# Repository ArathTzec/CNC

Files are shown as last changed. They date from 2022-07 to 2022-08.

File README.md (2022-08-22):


<h1 align="center"> ⚙️ MEJORA EN LA MANUFACTURA DE PLACAS PBC A TRAVÉS DE UNA MAQUINA CNC PARA ALUMNOS DE TSU EN MECATRÓNICA DENTRO DE LA UTEZ ⚙️ </h1>
<h3 align="center">🚀 Ing. de proyectos 🚀</h3>
<h4> Integrantes: </h4> 
<p>- 👷‍♂️ ARZATE VALLE JOSE MARTÍN </p>  
<p>- 👷‍♂️ FLORES FIGUEROA ALEJANDRO </p> 
<p>- 👷‍♂️ REYES ARAUJO ALDO </p> 
<p>- 👷‍♂️ ROQUE MORALES ALEJANDRO </p> 
<p>- 👷‍♂️ TZEC VARGAS ARATH </p>

### CONTENIDO
#### Descripción del proyecto
- 📚 Resumen
- 🏢 Planteamiento del problema 
- ⚙️ Objetivos
  - General 
  - Específicos 
- Justificación
- Alcances
#### Desarrollo
- 📎 Planeación
- Desarrollo del proyecto
  - Definición del proyecto
  - ✍ Boceto
  - 💰 Presupuesto estimado del proyecto
  - 🔨 Definición de partes mecánicas
  - 💻 Investigación de software de calibración de motores
  - 🖊 Diseño en SolidWorks
  - 💲 Compra de materiales
  - ✂ Cortar los perfiles de aluminio
  - 🖨 Impresión de piezas 3D
  - 👁 Verificar y corregir tolerancias de las piezas impresas
  - 🤏 Ajuste y lubricacion de ejes, rodamientos, guias, etc
  - 🔩 Configuracion, calibracion e instalacion del firmware/software
  - ✔ Prueba de funcionamiento 
#### Resultados y conclusiones 
- Resultados
  - Conclusiones y recomendaciones   

<h4 align="center"> DESCRIPCIÓN DEL PROYECTO </h4> 

##### 📚 Resumen 
<p>Actualmente las máquinas CNC se encuentran en una infinidad de aplicaciones a lo largo y ancho del planeta, desde la fabricación de electrodomésticos, pasando por la ebanistería hasta la producción de piezas para automóviles y aviones. Los beneficios de este tipo de tecnología son muchos, tales como: alta precisión en el fresado, permite mecanizar piezas más complejas, alta repetibilidad, los ajustes iniciales son mínimos y reduce al máximo los errores cometidos por el operario, a la vez que no requiere mucha habilidad por parte del mismo. </p> 
<p>Con la creación del prototipo de una máquina-herramienta CNC para el fresado y perforado automático de PCB, se brinda una calidad final muy alta a un costo de fabricación y esfuerzo muy bajo. </p>
<p>La máquina será de gran ayuda para los estudiantes de ingeniería en mecatrónica y todo tipo de personas que se dediquen al desarrollo de productos electrónicos, debido a que les permitirá llevar fácilmente sus circuitos desde la protoboard hasta la placa de impreso, en un tiempo de producción bastante corto. Por lo tanto, desde el punto de vista funcional, económico, y académico práctico, se confirma como necesario la sistematización del proceso de fabricación de placas de circuito impreso. </p>

##### 🏢 Planteamiento del problema
<p>Las PCB son una pieza fundamental en el montaje final de todo tipo de desarrollo tecnológico, ya que permite darle firmeza al circuito y darle una presentación adecuada, lamentablemente cuando los estudiantes requieren llevar de la protoboard a una PCB sus desarrollos se realiza de manera artesanal como el serigrafiado el cual es un método muy costoso, otro método es el de planchado el cual requiere demasiado tiempo y el peor de los casos dibujar manualmente el circuito sobre la placa. Por supuesto el resultado final deja mucho que desear, ya que no es muy presentable o incluso se pueden generar cortocircuitos que no se observaron y por supuesto el uso de cloruro férrico el cual es nocivo para la salud y el medio ambiente. </p> 

##### 🏹 Objetivos

###### General
- Crear una CNC que nos permita hacer PCBs de manera más precisa y con riesgo de falla mínimo.
###### Específicos 
- Realizar el diseño de cada una de las partes que conformarán la CNC.
Realizar la programación de la máquina-herramienta CNC, para fresar y perforar PCB de forma automática.

##### Justificación
<p>La razón de este proyecto es para que los estudiantes puedan pasar el desarrollo de sus circuitos en protoboard a una placa de circuito impreso con riesgo de falla mínimo, mas preciso, barato y en el menor tiempo posible, ya que los métodos empleados actualmente son muy costosos, requieren de mucho tiempo y se usan sustancias nocivas para la salud, por otro lado, la posibilidad de falla por cortocircuito es mayor debido a que en muchos casos no es posible apreciar a simple vista los errores cometidos. </p> 

##### Alcances
<p>Con este proyecto se pretende diseñar, construir y programar un prototipo de máquina fresadora y perforadora para la elaboración automática de placas de circuito impreso, utilizando para ello el control numérico por computador (CNC). La máquina es capaz de fresar placas de una dimensión máxima de 15x25cm, para ello se utilizan motores paso a paso con una resolución de 200 pasos por vuelta en configuración de paso completo. EI intercambio de herramientas en la máquina se realiza de forma manual, ya que por el reducido número de herramientas necesarias para el fresado y perforado de las PCB, no se hace necesario implementar un intercambiador automático.<p>
  
<h4 align="center"> DESARROLLO </h4> 

##### Planeación
<p>En la siguiente tabla se presenta el Diagrama de Gantt de las actividades a realizar en el proyecto.<p>
 
 |       Actividad       | S1 | S2 | S3 | S4 | S5 | S6 | S7 | S8 | S9 | S10 | S11 | S12 | S13 | S14 |
 |-----------------------|----|----|----|----|----|----|----|----|----|-----|-----|-----|-----|-----|
 |Definición de proyecto | X  |    |    |    |    |    |    |    |    |     |     |     |     |     |
 |Elección de proyecto   |    | X  |    |    |    |    |    |    |    |     |     |     |     |     |
 |Boceto del proyecto    |    |    | X  |    |    |    |    |    |    |     |     |     |     |     |
 |Presupuesto            |    |    | X  |    |    |    |    |    |    |     |     |     |     |     |
 |Inv. software de motores|   |    |    | X  | X  |    |    |    |    |     |     |     |     |     |
 |Diseño en SolidWorks   |    |    |    |    | X  | X  | X  |    |    |     |     |     |     |     |
 |Compra de materiales   |    |    |    |    | X  | X  |    |    |    |     |     |     |     |     |
 |Cortar perfiles de aluminio| |   |    |    |    |    | X  |    |    |     |     |     |     |     |
 |Impresión de piezas 3D      |    |    |    |    |    |    | X  |    |     |     |     |     |     |
 |Verificar y corregir tolerancias| | | |    |    |    |    | X  |    |     |     |     |     |     |
 |Ensamble de la CNC     |    |    |    |    |    |    |    |    | X  |     |     |     |     |     |
 |Ajuste y lubricación   |    |    |    |    |    |    |    |    |    |  X  |     |     |     |     |
 |Configuración e instalación de firmware/software|||||||   |    |    |     |  X  |     |     |     |
 |Entrega                |    |    |    |    |    |    |    |    |    |     |     |     |     |  X  |
  
##### Desarrollo del proyecto
<p>En esta sección se describe paso a paso todo el procedimiento que se llevó a cabo para el diseño de una CNC con el objetivo de mejorar la manufactura de PCBs y reducir los riesgos de falla.<p>

###### Definición de proyecto
<p>Para comenzar en la realización de este proyecto se pensó en una máquina que diera solución alguna problemática y se eligieron a los integrantes adecuados para formar un equipo de alto rendimiento.<p>

###### Elección de proyecto
 <p>Ya que hemos definido hacia dónde va el proyecto, se dieron varias propuestas que se muestran a continuación:<p>
   
  |         Integrante        |                Prouesta               |
  |---------------------------|---------------------------------------|
  | Arzate Valle Jose Martín  | *Maquina CNC*                         |
  | Flores Figueroa Alejandro | Sistema de llenado y sellado de bolis |
  | Reyes Araujo Aldo         | Protección para soldadura de mano     |
  | Roque Morales Alejandro   | Sistema de enfriamiento de hielera    |
  | Tzec Vargas Arath         | Compuerta automática para perros      |
   
###### ✍ Boceto
Esta imagen representa el boceto realizado en el software de SolidWorks, de aquí partimos para poder realizarlo en físico

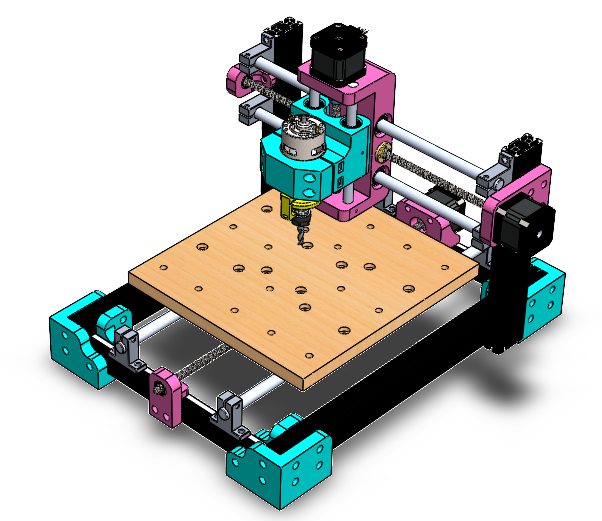
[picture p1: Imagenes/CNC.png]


###### 💰 Presupuesto estimado del proyecto
Aqui podras encontrar el presupuesto y material del proyecto ===> [Presupuesto](https://github.com/ArathTzec/CNC/tree/main/Materiales)
   
###### 💻 Investigación de software de calibración de motores
<p>GRBL es un firmware para el control de máquinas CNC, está pensado para usarse en placas Arduino con un microcontrolador Atmega328, ya que nos permite configurar el control y desplazamiento de nuestra máquina. Los controladores paso a paso se clasifican para una longitud de impulso mínima de paso.<p>
  
###### 🖊 Diseño en SolidWorks
<p>Para realizar el proyecto de manera física, primero se requiere un diseño que ayudará para evitar problemas y proporcionar parámetros para optimizar aspectos cruciales del proyecto. A continuación, se muestra el diseño en el programa SolidWorks:<p>
  
###### 💲 Compra de materiales
<p>Se realizó la compra de los materiales listados anteriormente por medio de tiendas en línea como lo fueron Amazon y Mercado Libre, en la siguiente figura se muestra el material comprado.<p>
  
###### ✂ Cortar perfiles de aluminio
<p>Se cortaron los perfiles de aluminio en medidas de:
  - 2 perfiles de 40 cm
  - 2 perfiles de 25.5 cm
  - 2 perfiles de 24 cm<p>
    
###### 🖨 Impresión de piezas 3D

Las piezas se imprimieron mediante impresora 3D, para más información dirígete al siguiente enlace ===> [Piezas en 3D](https://github.com/ArathTzec/CNC/tree/main/Archivos%20CAD/M%C3%A1quina%20CNC)
  
###### 👁 Verificar y corregir tolerancias de las piezas impresas

Todas las piezas que se imprimen en 3D llegan a tener alguna tolerancia o “error” de impresión, para corregir este error puedes lijar la pieza impresa hasta que los elementos como rodamientos, guías, husillos y tornillos logren entrar correctamente 

###### 🤏 Ajuste y lubricación de ejes, rodamientos, guias, etc.

Para lubricar los componentes se utilizó grasa blanca con litio y aceite. Las siguientes imagenes muestran la colocacion de estos: 

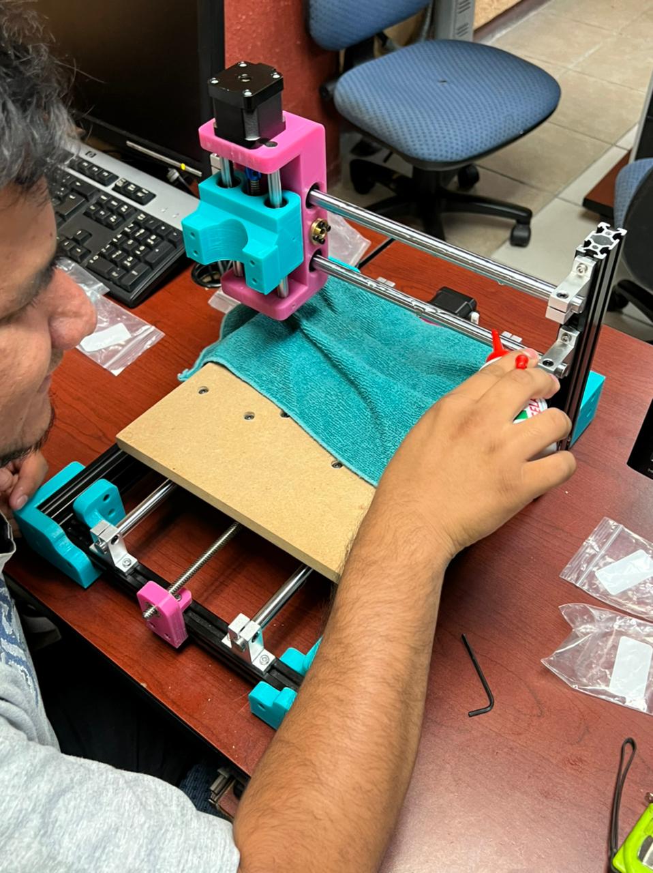
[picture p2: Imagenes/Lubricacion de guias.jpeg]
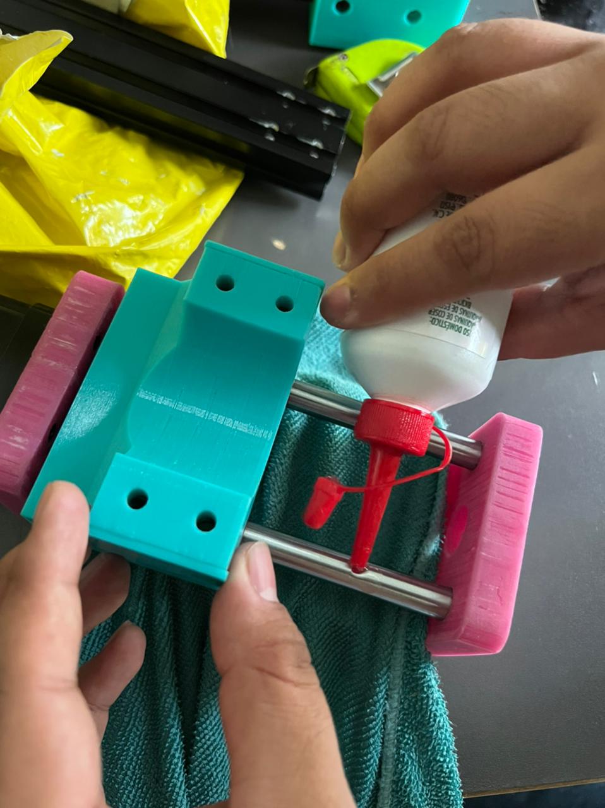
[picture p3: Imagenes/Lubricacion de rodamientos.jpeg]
    

###### 🔩 Configuracion, calibracion e instalacion del firmware/software
 
Puedes consultar como se calibro dando click aqui ==> [Calibracion](https://github.com/ArathTzec/CNC/blob/main/Manuales/Configuracion%20de%20los%20drivers%20para%20el%20motor%20paso%20a%20paso%20.pdf)
 
###### ✔ Prueba de funcionamiento 
En la primera prueba se volvieron a ajustar los motores, debido a que no estaban bien calibrados. También se agrego mas grasa blanca con litio para que los husillos funcionaran de una mejor manera, ya con esta grasa los ejes se pudieron mover correctamente. De la misma manera al hacer estos cambios la maquina funciono mejor 
 
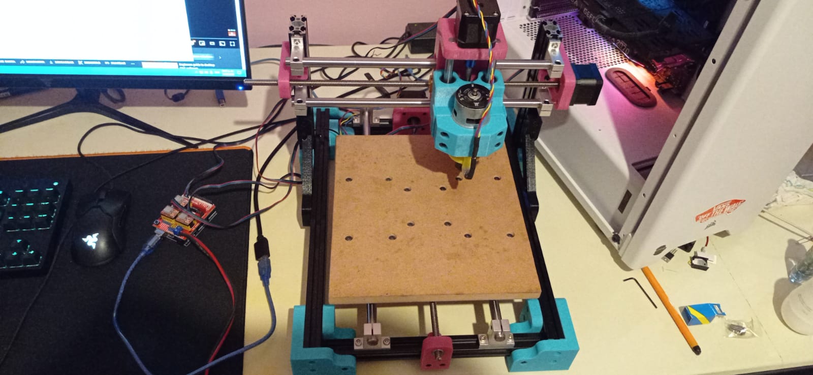
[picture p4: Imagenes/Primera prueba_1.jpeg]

 
##### Entrega de proyecto
 
<h4 align="center"> RESULTRADOS Y CONCLUSIONES </h4> 

Como resultados del proyecto se entrego una maquina CNC que logra mejorar la manofactura de las placas PCB:

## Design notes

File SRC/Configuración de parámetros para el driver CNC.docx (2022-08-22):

Configuración de parámetros para el driver CNC -GRBL

El driver GRBL necesita una configuración previa para funcionar y tener la mejor precisión posible, para esto se configurarán los parámetros del $0 -$22, cabe mencionar que algunos parámetros se colocaron de default.

Dependiendo del motor a pasos que se compró, se buscó el datasheet para visualizar los grados por paso que da el motor, este motor cuenta con 1.8°, pero necesitamos saber cuantos pasos requiere para dar una vuelta, por lo tanto, se tiene lo siguiente:

((un giro completo)360)/1.8=Se requieren de 200 pasos para una vuelta completa

Lo que sigue después es saber dependiendo de la varilla, cuantos milímetros se recorre por cada vuelta, por lo tanto, para las varillas que se compraron se tiene que por cada vuelta recorre 8 milímetros, cuando se divide entre el numero de pasos para dar la vuelta completa del motor queda en 25.

De esta manera se colocan los parámetros del $0 al $3 que corresponden a los pasos por milímetros de los motores x, y z

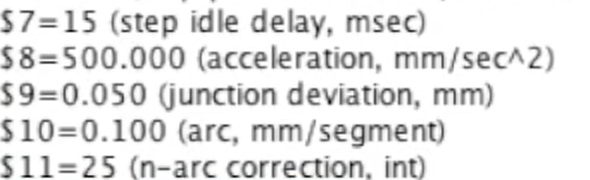
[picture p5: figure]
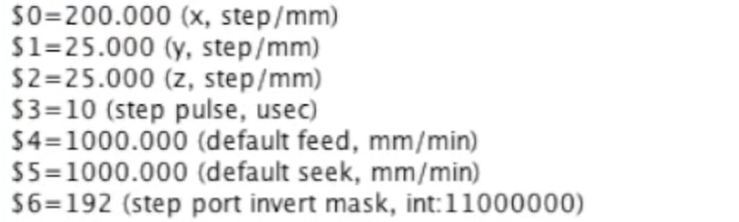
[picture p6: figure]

Después configurar el ancho de pulso que manda el Arduino, se colocó en 10

- Los puntos 4 y 5 corresponden a velocidad del motor, en este caso es de 1000
- 6 no se modifica nada
- 7 es el tiempo de retardo después de realizar alguna orden, se coloco en 15 milisegundos
- 8 la aceleración del motor quedo en 500 debido a que a esa aceleración el motor dejo de vibrar
- 9-11 Se quedaron en default. En el numero 12 se colocaron 3 decimales para mayor precisión.
- 13 se configura todo en milímetros colocando un 1
- 14-18 Default
- 19-20 Se configura la velocidad con la que la maquina vuelve al origen
- 21-22 Default

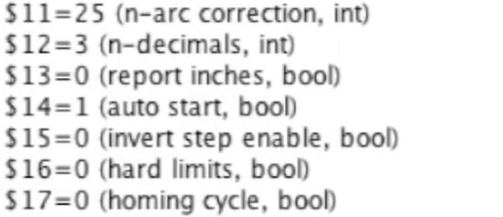
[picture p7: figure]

- La lista queda de la siguiente manera:

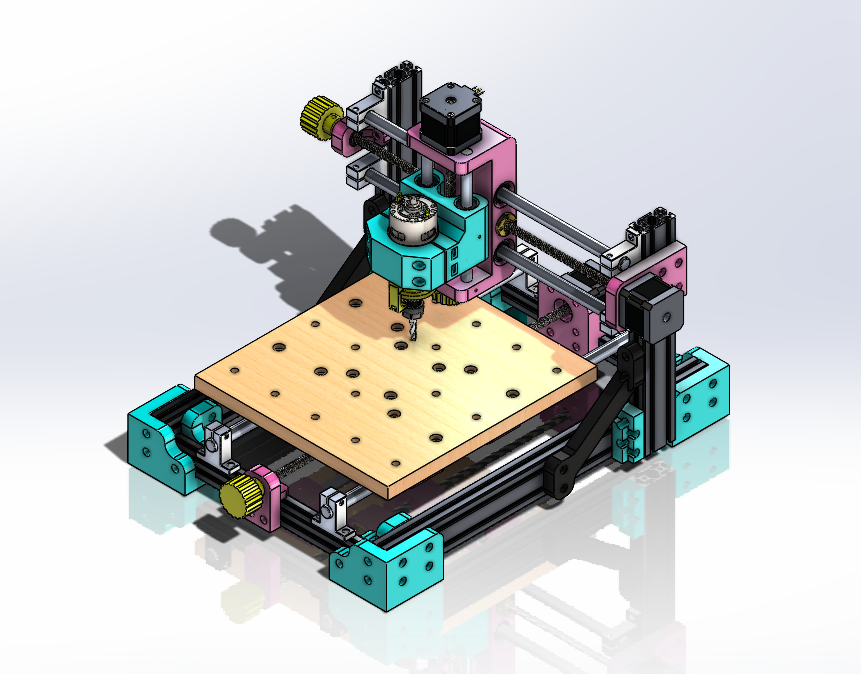
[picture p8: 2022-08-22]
Imagenes/Diseño terminado.PNG

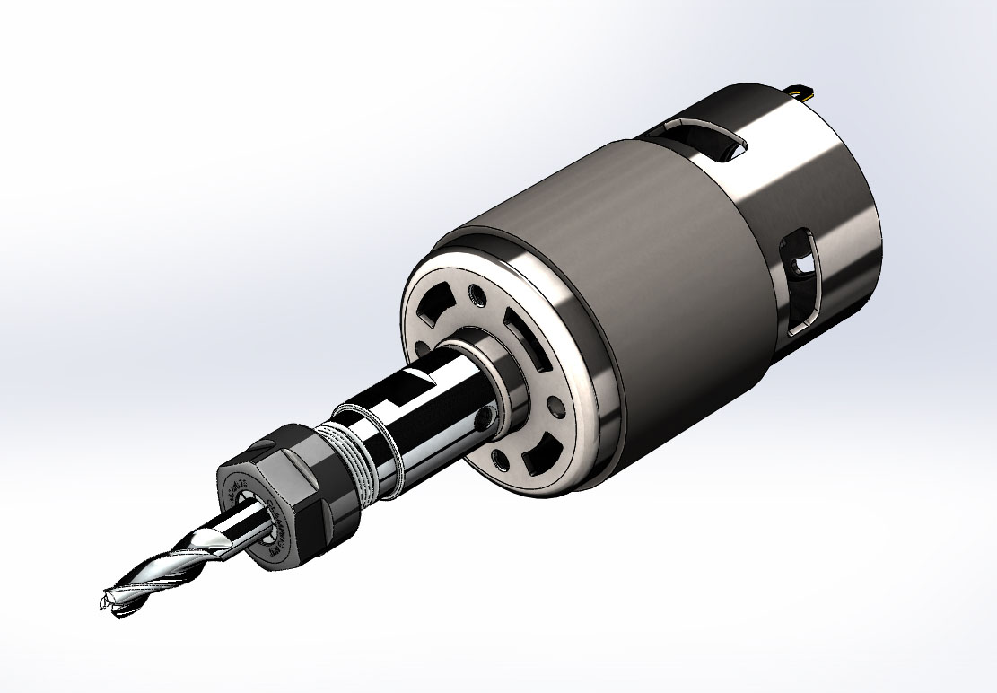
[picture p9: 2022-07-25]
Archivos CAD/Máquina CNC V1.1/Source/Motor CD/Motor - RS-775 - 1.JPG

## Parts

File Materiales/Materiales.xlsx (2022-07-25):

LISTA DE MATERIALES Y PRECIOS DEL PROYECTO
Material | Cantidad | Precio Unitario | Total
Motor DC 755 | 1 | $748 | $748
Motor a pasos | 3 | $170 | $510
Rollo de PETG 1.75mm 1KG | 1 | $449 | $449
Fuente de alimentación 24V | 1 | $409 | $409
Base soporte para riel eje lineal | 4 | $55 | $220
Rodamiento LM12UU | 8 | $65 | $520
Guía lineal 8mm 300mm | 1 | $110 | $110
Perfil aluminio 2080 500mm | 1 | $650 | $650
Perfil de aluminio 2040 400mm | 2 | $258 | $516
Perfil de aluminio 2020 300mm | 6 | $85 | $510
Guía lineal 12mmX1500mm | 1 | $575 | $575
Guía lineal 10mmX300mm | 1 | $230 | $230
Sensor de velocidad | 1 | $150 | $150
Tabla de madera 240mmX160mm | 1 | $200 | $200
Total: |  |  | $5797

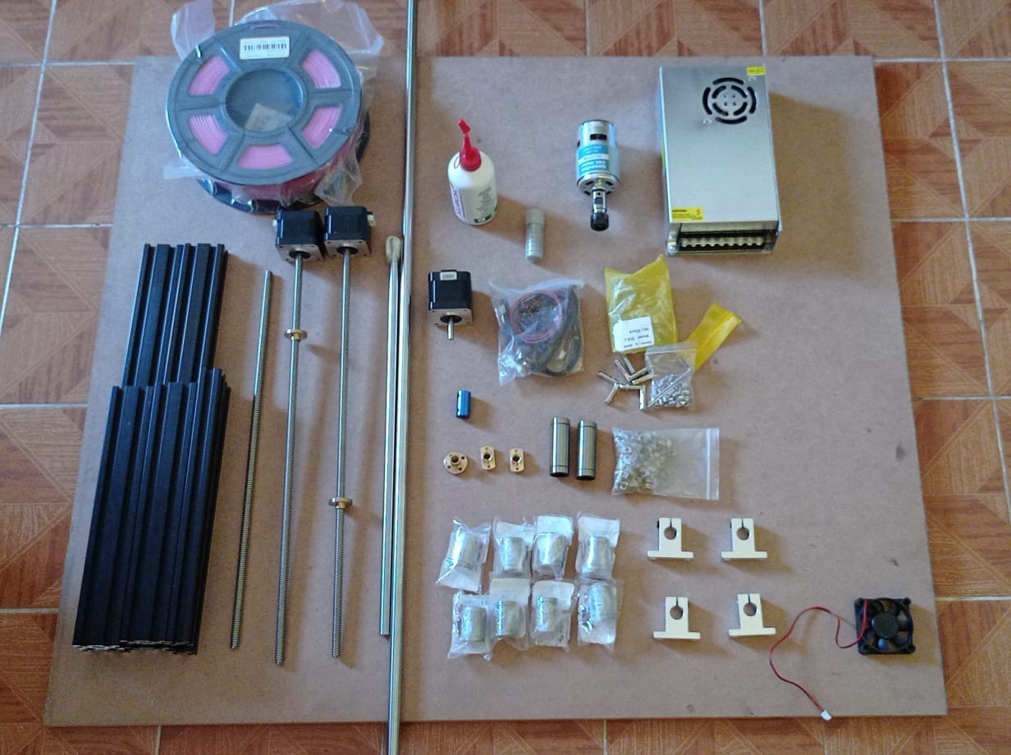
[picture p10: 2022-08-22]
Materiales/Materiales.jpeg

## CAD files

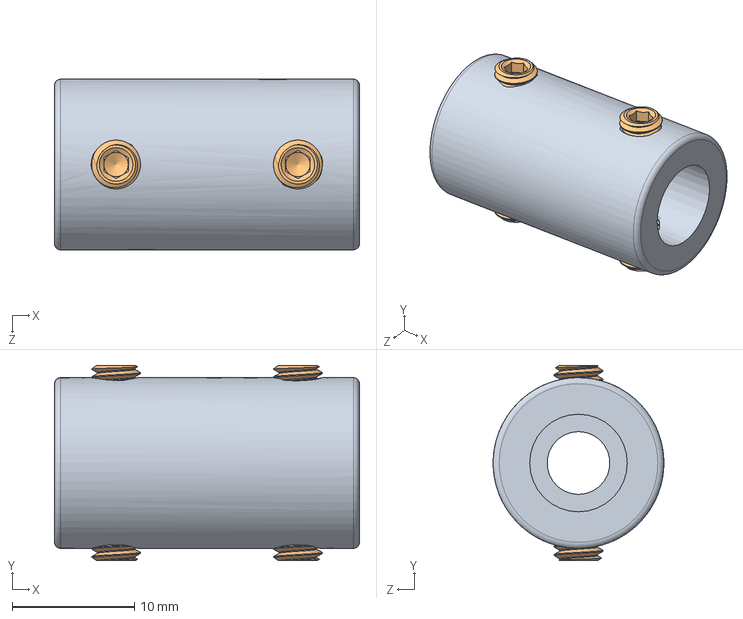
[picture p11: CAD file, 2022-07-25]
Archivos CAD/Máquina CNC V1.1/Source/Shaft Coupler_5 - 8 mm.SLDASM
25.0 x 16.0 x 14.0 mm
Shaft Coupler.step
M4 x 4mm Cup-Point Set Screw.step x 4

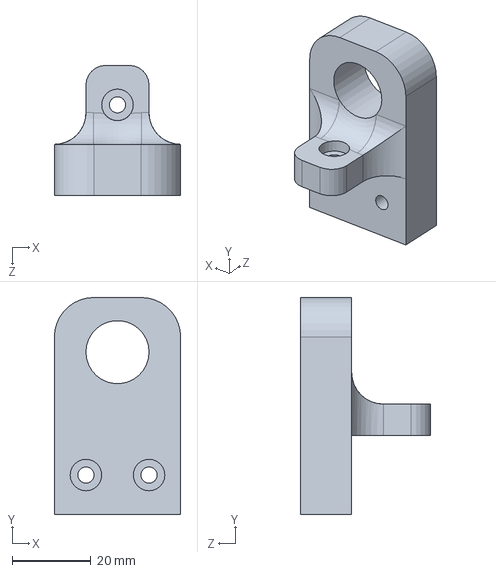
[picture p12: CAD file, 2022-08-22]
Archivos CAD/Máquina CNC V1.1/Base rodamiento Y.SLDPRT
32.0 x 55.0 x 33.0 mm

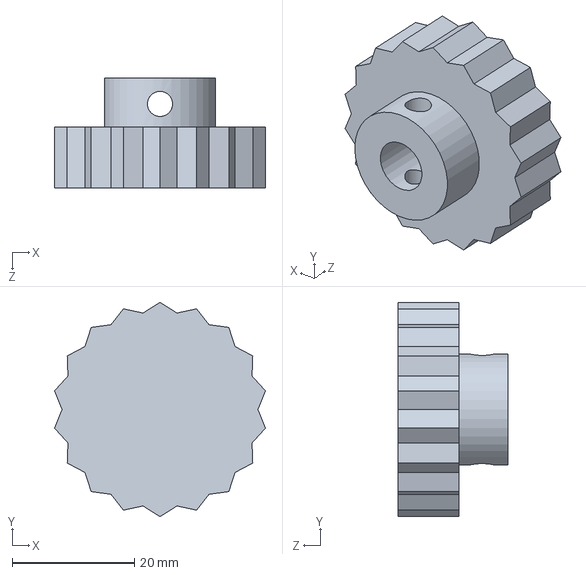
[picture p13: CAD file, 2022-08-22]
Archivos CAD/Máquina CNC V1.1/Source/Tuerca de ajuste eje Z.SLDPRT
34.5 x 35.0 x 18.0 mm

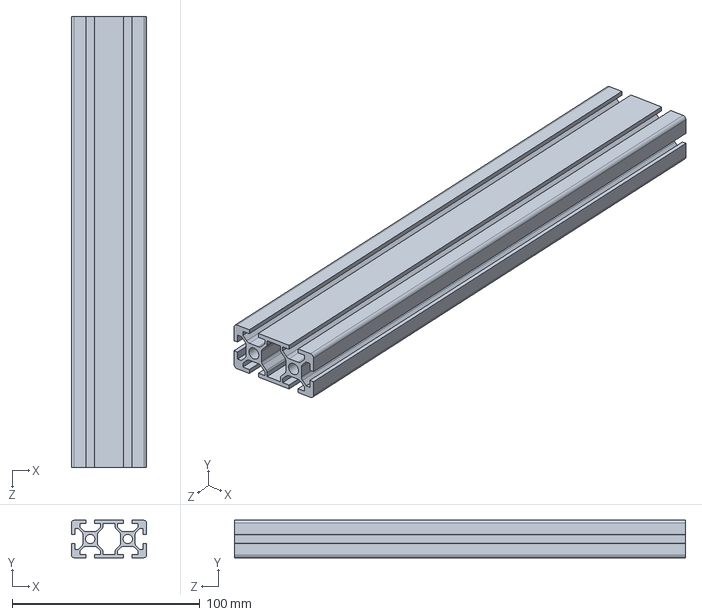
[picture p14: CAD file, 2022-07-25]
Archivos CAD/Máquina CNC V1.1/Perfil 2040 - 180mm.SLDPRT
40.0 x 20.0 x 240.0 mm

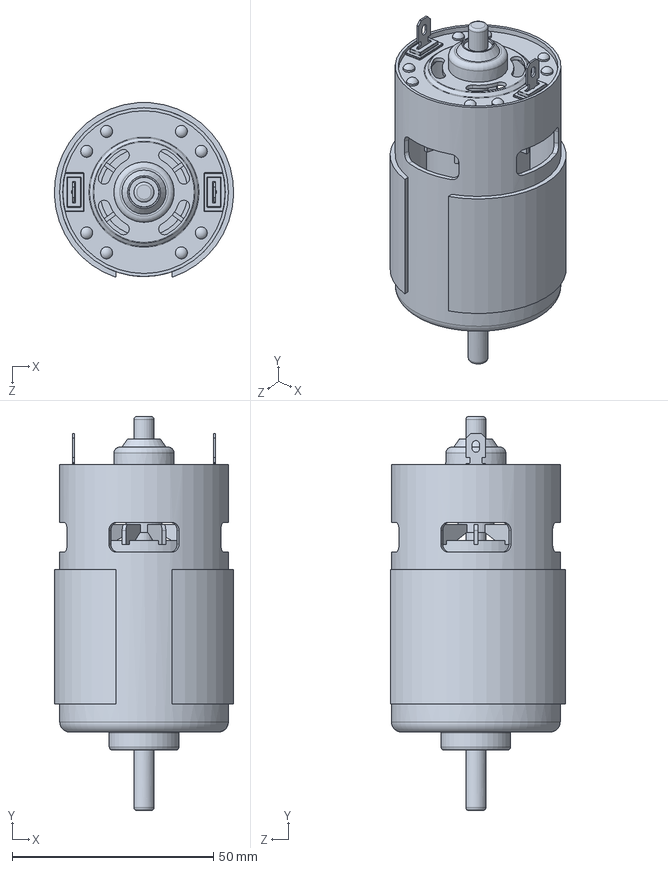
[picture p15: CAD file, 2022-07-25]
Archivos CAD/Máquina CNC V1.1/Source/Motor CD/Motor - RS-775.SLDPRT
44.6 x 98.0 x 43.4 mm

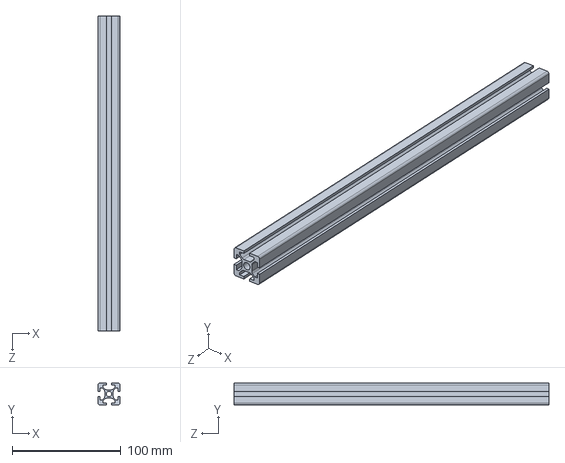
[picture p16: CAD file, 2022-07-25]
Archivos CAD/Máquina CNC V1.1/Perfil 2020 - 240mm.SLDPRT
20.0 x 20.0 x 290.0 mm

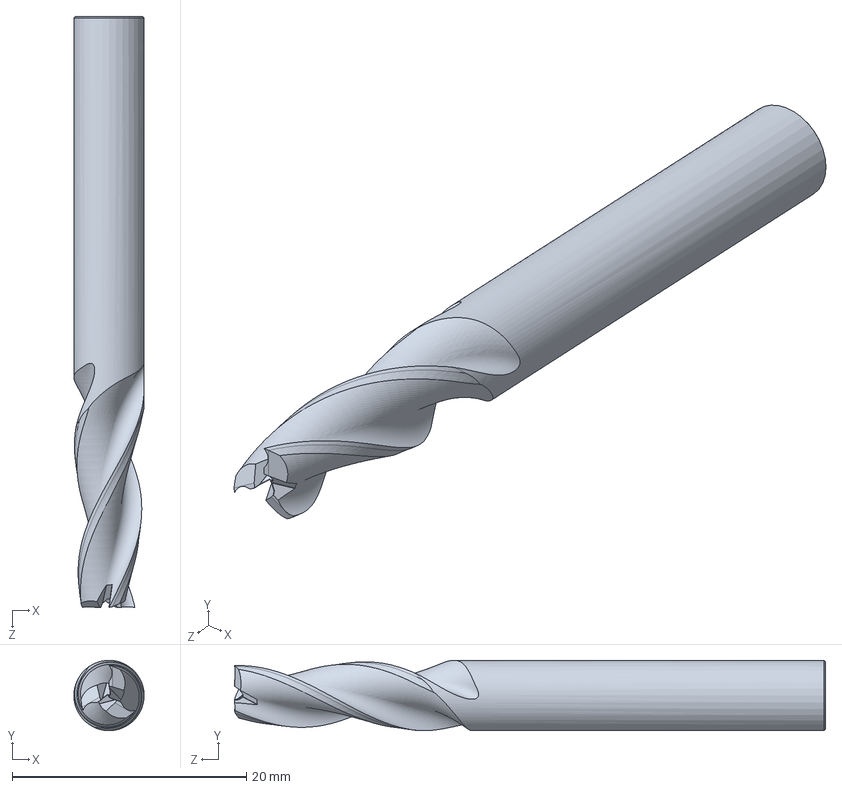
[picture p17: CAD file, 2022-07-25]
Archivos CAD/Máquina CNC V1.1/Source/Motor CD/Фреза.SLDPRT
6.00 x 6.00 x 50.4 mm

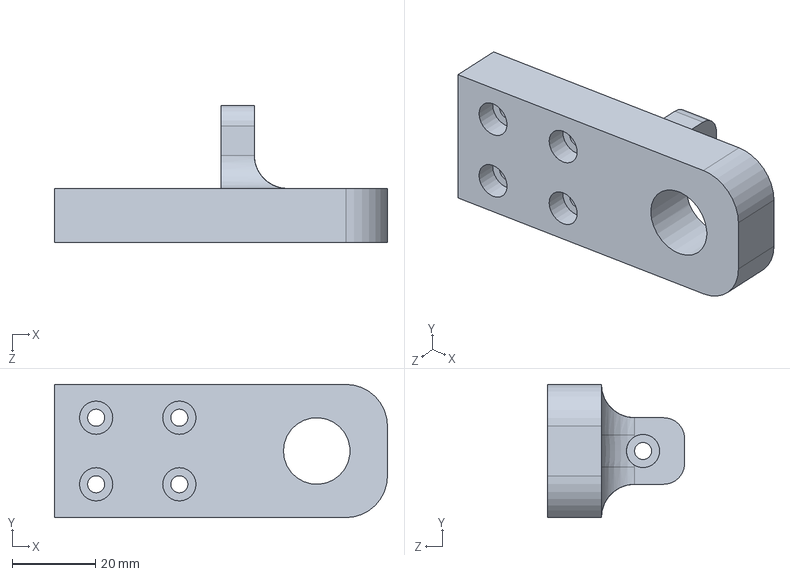
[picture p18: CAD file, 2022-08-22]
Archivos CAD/Máquina CNC V1.1/Source/Soporte rodamiento X.SLDPRT
80.0 x 32.0 x 33.0 mm

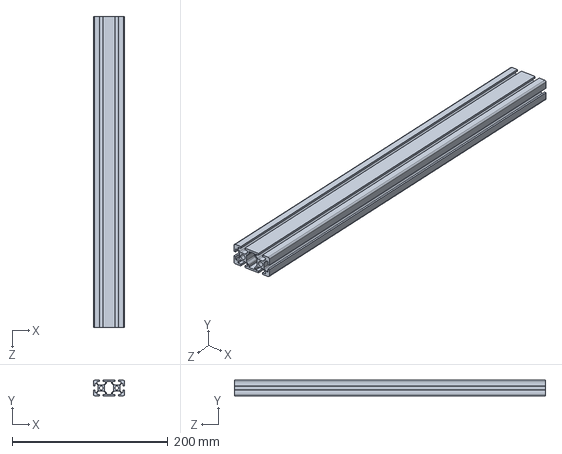
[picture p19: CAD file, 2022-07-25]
Archivos CAD/Máquina CNC V1.1/Perfil 2040.SLDPRT
40.0 x 20.0 x 400.0 mm

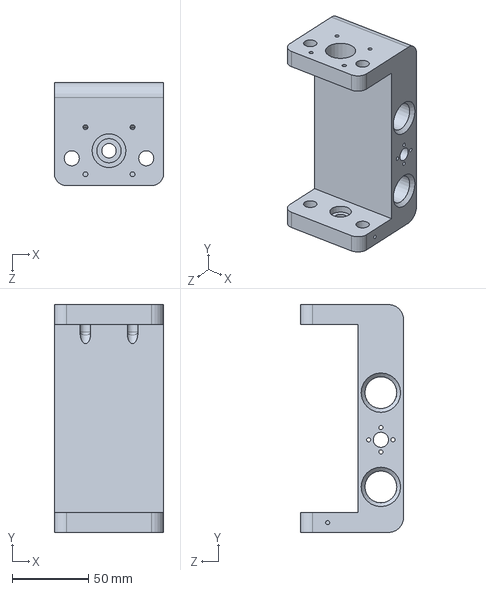
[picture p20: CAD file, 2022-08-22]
Archivos CAD/Máquina CNC V1.1/Source/Holder axis x-z.SLDPRT
72.0 x 150.0 x 68.0 mm

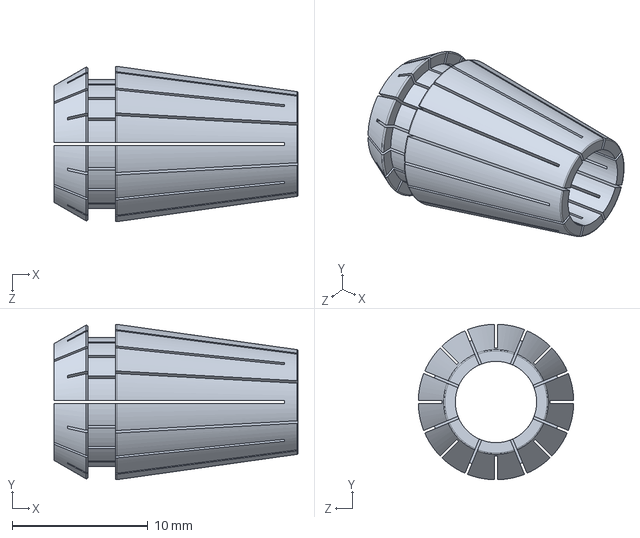
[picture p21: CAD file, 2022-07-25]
Archivos CAD/Máquina CNC V1.1/Source/Motor CD/COLLET ER11 d6-.SLDPRT
18.0 x 11.5 x 11.5 mm

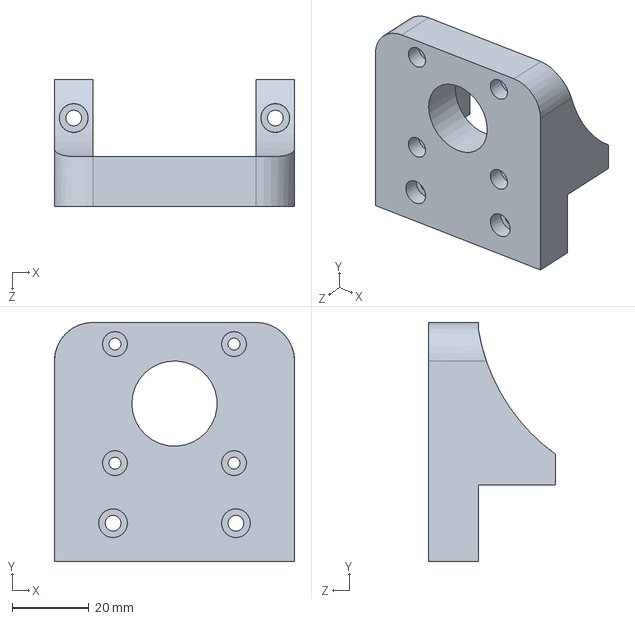
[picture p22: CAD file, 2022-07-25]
Archivos CAD/Máquina CNC V1.1/Base motor Y.SLDPRT
62.5 x 62.3 x 33.0 mm

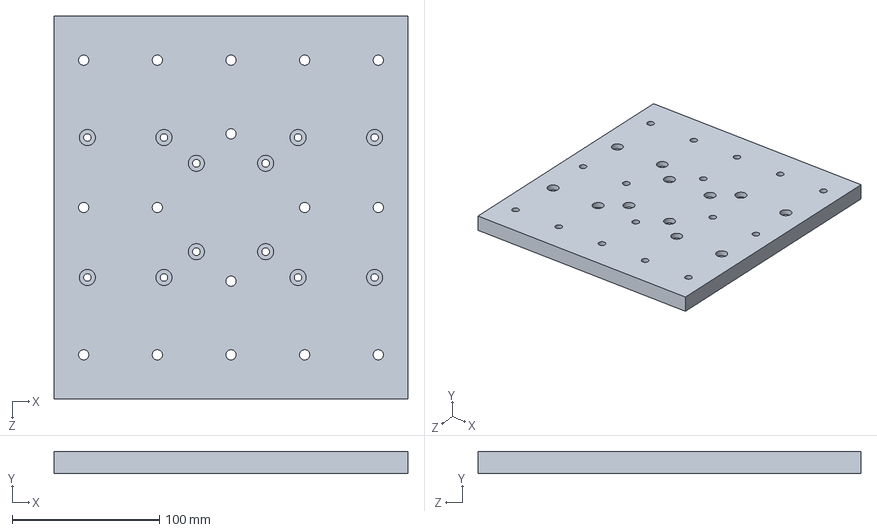
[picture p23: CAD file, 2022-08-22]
Archivos CAD/Máquina CNC V1.1/Source/Base Madera.SLDPRT
240.0 x 15.0 x 260.0 mm

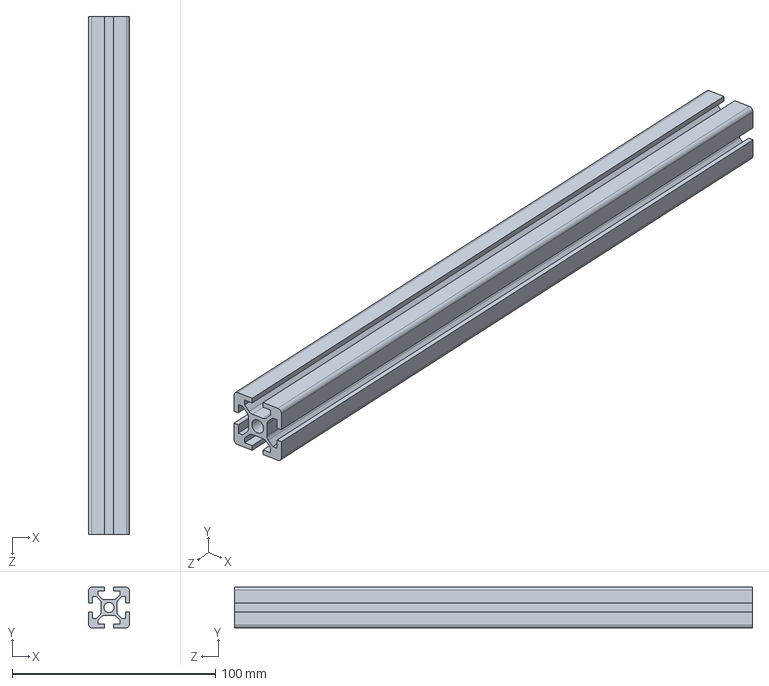
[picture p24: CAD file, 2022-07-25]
Archivos CAD/Máquina CNC V1.1/Perfil 2020.SLDPRT
20.0 x 20.0 x 255.0 mm

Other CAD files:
Archivos CAD/Máquina CNC V1.1/Source/SimetríaAngulo perfil X-Z.SLDPRT
Archivos CAD/Máquina CNC V1.1/Source/Angulo de soporte.SLDPRT
Archivos CAD/Máquina CNC V1.1/Source/Tuerca de ajuste eje X.SLDPRT
Archivos CAD/Máquina CNC V1.1/Source/SimetríaSimetríaSoporte esquina.SLDPRT
Archivos CAD/Máquina CNC V1.1/Source/Angulo perfil X-Z.SLDPRT
Archivos CAD/Máquina CNC V1.1/Source/Axis Z soporte motor.SLDPRT
Archivos CAD/Máquina CNC V1.1/Source/Ball Bearing 8 x 16 x 5.SLDPRT
Archivos CAD/Máquina CNC V1.1/Source/Base de goma.SLDPRT
Archivos CAD/Máquina CNC V1.1/Source/Base imanes.SLDPRT
Archivos CAD/Máquina CNC V1.1/Source/Base sensor cny70.SLDPRT
Archivos CAD/Máquina CNC V1.1/Source/Guia - Eje X.SLDPRT
Archivos CAD/Máquina CNC V1.1/Source/Guia 10mm.SLDPRT
Archivos CAD/Máquina CNC V1.1/Source/Guia.SLDPRT
Archivos CAD/Máquina CNC V1.1/Source/Holder axis y.SLDPRT
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

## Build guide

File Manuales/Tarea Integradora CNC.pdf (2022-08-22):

## UNIVERSIDAD TECNOLÓGICA EMILIANO ZAPATA DEL ESTADO DE

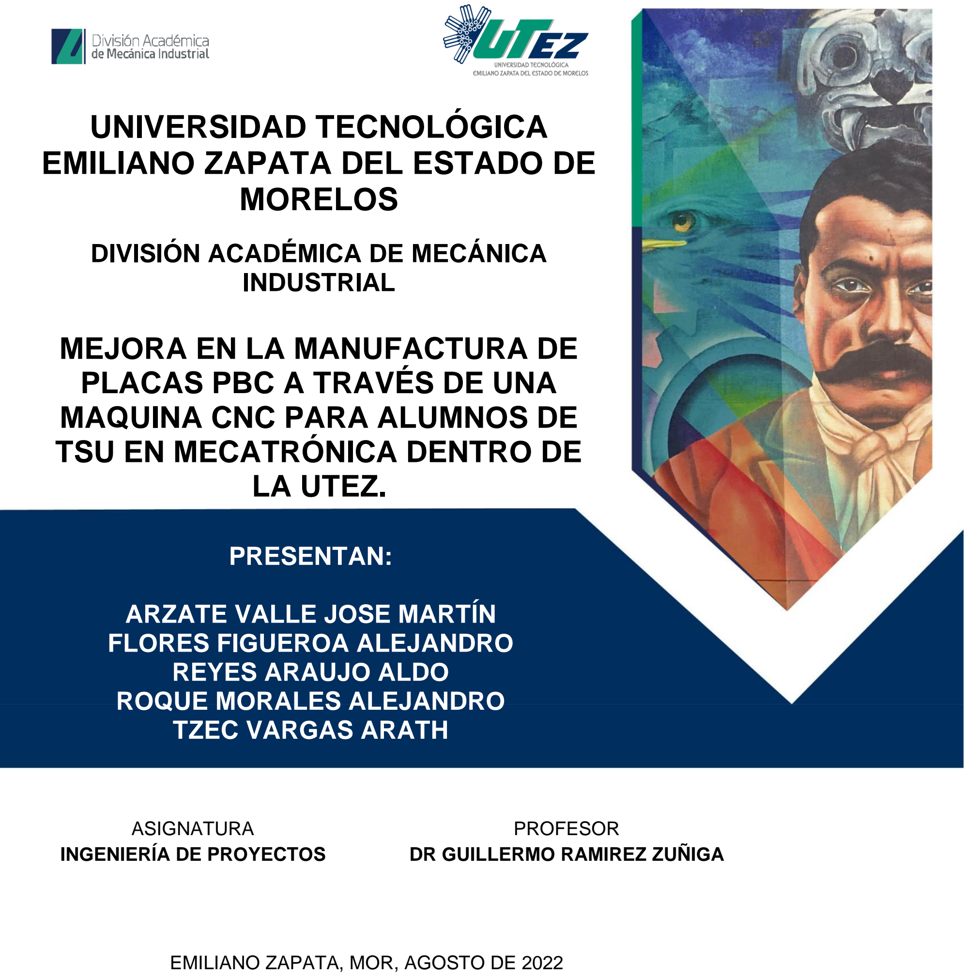
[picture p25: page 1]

ASIGNATURA | PROFESOR
INGENIERÍA DE PROYECTOS | DR GUILLERMO RAMIREZ ZUÑIGA

## PRESENTAN:

## ARZATE VALLE JOSE MARTÍN FLORES FIGUEROA ALEJANDRO REYES ARAUJO ALDO ROQUE MORALES ALEJANDRO TZEC VARGAS ARATH

EMILIANO ZAPATA, MOR, AGOSTO DE 2022

## MORELOS

## DIVISIÓN ACADÉMICA DE MECÁNICA INDUSTRIAL

## MEJORA EN LA MANUFACTURA DE PLACAS PBC A TRAVÉS DE UNA MAQUINA CNC PARA ALUMNOS DE TSU EN MECATRÓNICA DENTRO DE

LA UTEZ.

## CONTENIDO

Índice de figuras

Índice de tablas

Resumen

REFERENCIAS

## ÍNDICE DE FIGURAS

Figura 4.4 Soportes base eje Y | 23
Figura 4.5 Soporte Motor | 23
Figura 4.6 Soportes de los husillos | 23
Figura 4.7 Rodamiento eje Y | 23
Figura 4.8 Rodamiento en eje Z | 23
Figura 4.9 Rodamientos eje X | 23
Figura 4.10 Maquina CNC ensamblada | 24
Figura 4.11 Lubricación eje Z | 25
Figura 4.12 Lubricación eje X | 25
Figura 4.13 Identificación de alimentación en el driver | 26
Figura 4.14 Visualización de voltaje necesario para calibración | 26
Figura 4.15 Ajuste de resistencia | 27
Figura 4.16 Conexión de motores al driver | 27
Figura 4.17 Pruebas a los motores | 28
Figura 4.18 Driver empleado | 28
Figura 4.19 Valor de los pasos | 30
Figura 4.20 Velocidad por eje | 30
Figura 4.21 Aceleración por eje | 31
Figura 4.22 Distancias máximas | 31
Figura 4.23 Lista de configuraciones | 31
Figura 4.24 Prueba de funcionamiento | 32

## ÍNDICE DE TABLAS

Tabla 3.1 Diagrama de Gantt | 11
Tabla 3.2 Tabla de propuestas | 12
Tabla 3.3 Tabla de presupuesto | 13
Tabla 4.1 Tabla de coste final del proyecto | 21
Tabla 4.2 Tabla de configuración de pasos | 29

## RESUMEN

Actualmente las máquinas CNC se encuentran en una infinidad de aplicaciones a lo

largo y ancho del planeta, desde la fabricación de electrodomésticos, pasando por la

ebanistería hasta la producción de piezas para automóviles y aviones. Los beneficios

de este tipo de tecnología son muchos, tales como: alta precisión en el fresado, permite

mecanizar piezas más complejas, alta repetibilidad, los ajustes iniciales son mínimos

y reduce al máximo los errores cometidos por el operario, a la vez que no requiere

mucha habilidad por parte del mismo.

Con la creación del prototipo de una máquina-herramienta CNC para el fresado y

perforado automático de PCB, se brinda una calidad final muy alta a un costo de

fabricación y esfuerzo muy bajo.

La máquina será de gran ayuda para los estudiantes de ingeniería en mecatrónica y

todo tipo de personas que se dediquen al desarrollo de productos electrónicos, debido

a que les permitirá llevar fácilmente sus circuitos desde la protoboard hasta la placa

de impreso, en un tiempo de producción bastante corto. Por lo tanto, desde el punto

de vista funcional, económico, y académico práctico, se confirma como necesario la

sistematización del proceso de fabricación de placas de circuito impreso.

Es por la relevancia de esta máquina y el uso que se tiene intencionado hacia ésta que

se ha decidido por optar la realización de un sistema que nos permita regular y

mantener en buen estado la temperatura del motor de la máquina, esto debido a la

importancia de este elemento dentro del funcionamiento de la máquina.

## CAPÍTULO 1.DESCRIPCIÓN DEL PROYECTO

### 1.1 Planteamiento del problema

Las PCB son una pieza fundamental en el montaje final de todo tipo de desarrollo

tecnológico, ya que permite darle firmeza al circuito y darle una presentación

adecuada, lamentablemente cuando los estudiantes requieren llevar de la protoboard

a una PCB sus desarrollos se realiza de manera artesanal como el serigrafiado el cual

es un método muy costoso, otro método es el de planchado el cual requiere demasiado

tiempo y el peor de los casos dibujar manualmente el circuito sobre la placa. Por

supuesto el resultado final deja mucho que desear, ya que no es muy presentable o

incluso se pueden generar cortocircuitos que no se observaron y por supuesto el uso

de cloruro férrico el cual es nocivo para la salud y el medio ambiente.

### 1.2 Objetivos

### 1.2.1 General

Crear una CNC que nos permita hacer PCBs de manera más precisa y con riesgo de

falla mínimo.

### 1.2.2 Específicos

Realizar el diseño de cada una de las partes que conformarán la CNC.

Realizar la programación de la máquina-herramienta CNC, para fresar y perforar PCB

de forma automática.

### 1.3 Justificación

La razón de este proyecto es para que los estudiantes puedan pasar el desarrollo de

sus circuitos en protoboard a una placa de circuito impreso con riesgo de falla mínimo,

más preciso, barato y en el menor tiempo posible, ya que los métodos empleados

actualmente son muy costosos, requieren de mucho tiempo y se usan sustancias

nocivas para la salud, por otro lado, la posibilidad de falla por cortocircuito es mayor

debido a que en muchos casos no es posible apreciar a simple vista los errores

cometidos.

### 1.4 Alcances

Con este proyecto se pretende diseñar, construir y programar un prototipo de máquina

fresadora y perforadora para la elaboración automática de placas de circuito impreso,

utilizando para ello el control numérico por computador (CNC). La máquina es capaz

de fresar placas de una dimensión máxima de 26x24cm, para ello se utilizan motores

paso a paso con una resolución de 200 pasos por vuelta en configuración de paso

completo. EI intercambio de herramientas en la máquina se realiza de forma manual,

ya que por el reducido número de herramientas necesarias para el fresado y perforado

de las PCB, no se hace necesario implementar un intercambiador automático.

### 1.5 Datos generales de la empresa

Nombre

Universidad Tecnológica Emiliano Zapata del Estado de Morelos

Logotipo

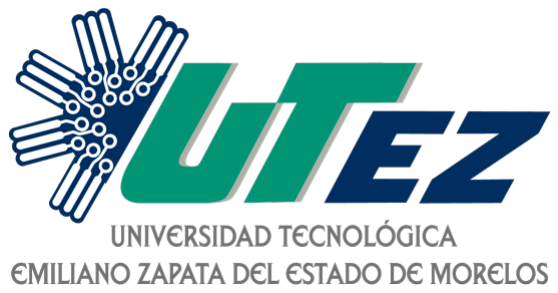
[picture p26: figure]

Figura 1.1 Logotipo de la UTEZ

Dirección

Av. Universidad Tecnológica 1, Palo Escrito, 62765 Emiliano Zapata, Mor.

Giro

Institución educativa

Asesor Institucional

Dr. Guillermo Ramírez Zúñiga

## CAPÍTULO 2.MARCO TEÓRICO

### 2.1 Revisión Bibliográfica

2.1.1 ¿Qué es una CNC?

El control numérico por computadora es un sistema que permite controlar en todo

momento la posición de un elemento físico.

En los procesos de mecanizado, se utiliza el CNC para controlar máquinas como

tornos CNC o fresadoras CNC y obtener así productos seriados totalmente

personalizados para el cliente final.

Figura 2.1 Maquinado en CNC

2.1.2 ¿Qué es un motor a pasos?

El motor paso a paso es un motor de corriente continua sin escobillas en el que la

rotación se divide en un cierto número de pasos resultantes de la estructura del motor.

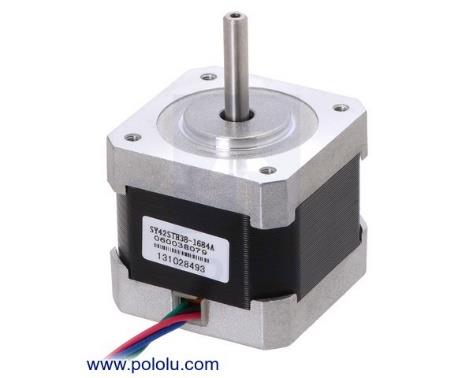
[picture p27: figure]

Figura 2.2 Motor a pasos

### 2.1.3 Rodamiento de tipo lineal modelo LM12UU

Fabricado a base de acero GCR15, además los balines que se encuentran en su

interior también son fabricados a base de este material, mediante un tratamiento

térmico para que el cromo se endurezca. Este accesorio es usado como guía de

precisión útil en maquinaría de alimentos, envasado, médica, impresión, textiles,

maquinas CNC o impresoras 3D.

Figura 2.3 Rodamiento LM12UU

2.1.4 ¿Qué es un acoplamiento?

Los acoplamientos o acoples mecánicos son elementos de una máquina que sirven

para prolongar líneas de transmisión de ejes o conectar tramos de diferentes ejes, en

planos diferentes o con dirección paralela, para transmitir energía

Figura 2.4 Acoplamiento

### 2.1.5 Sensor QRE1113

QRE1113 es un sensor óptico infrarrojo de reflexión de corto alcance. El sensor

QRE1113 posee un diseño compacto donde la fuente de emisión de luz (diodo IR) y el

detector (fototransistor) están dispuestos en la misma dirección. El diodo IR emite un

haz de luz infrarroja que al rebotar sobre una superficie reflectante (color blanco) es

detectado por el fototransistor, que a su vez el paso de corriente de forma proporcional

a la luz reflejada.

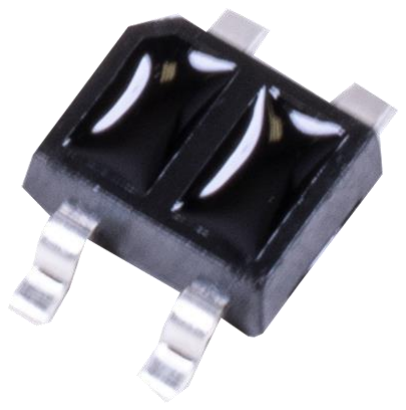
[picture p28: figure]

Figura 2.5 Sensor QRE1113

### 2.1.6 Arduino

Es una plataforma de desarrollo basada en una placa electrónica de hardware libre

que incorpora un microcontrolador re-programable y una serie de pines hembra. Estos

permiten establecer conexiones entre el microcontrolador y los diferentes sensores y

actuadores de una manera muy sencilla (principalmente con cables dupont).

Figura 2.6 Arduino

### 2.1.7 Driver A4988

El uso de un driver Pololu para el control de un motor paso a paso nos simplifica mucho

el trabajo ya que este driver se encarga de generar todas las señales necesarias para

su funcionamiento y además nos añade las protecciones necesarias de temperatura y

corriente. Otra ventaja que nos proporciona es que solo necesitaremos un par de

puertos del micro, en este caso Arduino para controlarlo todo, dejando más puertos

libres para otras funciones.

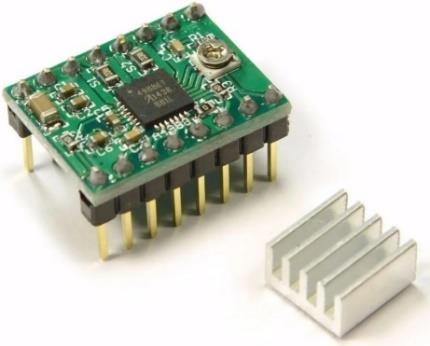
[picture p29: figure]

Figura 2.7 Driver A4988

### 2.1.8 Filamento PETG

Filamento de PETG. En lo que respecta a la impresión en 3D, el material PETG es la

versión particular de este plástico que se utiliza en los procesos de impresión en 3D,

mientras que la G significa «modificado con glicol».

Figura 2.8 Filamento PETG

### 2.1.9 Husillo

El husillo es un mecanismo destinado a transmitir el movimiento en ciertos elementos

de las fresadoras y otras máquinas industriales que, mediante un tornillo sinfín,

convierte un movimiento giratorio en un movimiento rectilíneo.

Figura 2.9 Husillo

## CAPÍTULO 3.DESARROLLO

### 3.1 Planeación

En la Tabla 3.1 se presenta el Diagrama de Gantt de las actividades a realizar en el

proyecto.

Tabla 3.1 Diagrama de Gantt

| Nombre del proyecto: Mejora en la manufactura de placas PBC a través de una maquina CNC para alumnos de TSU en mecatrónica dentro de la UTEZ. Periodo: Mayo - Agosto 2022
Actividad | MES | MAYO | JUNIO | JULIO | AGOSTO
SEMANA | 1 | 2 | 3 | 4 | 1 | 2 | 3 | 4 | 1 | 2 | 3 | 4 | 1 | 2 | 3 | 4

Definición de proyecto

Elección de proyecto

Boceto del proyecto elegido Presupuesto estimado del proyecto

Investigación de software de calibración de motores

Diseño en SolidWorks

Compra de materiales

Cortar los perfiles de aluminio

Impresión de piezas 3D

Verificar y corregir tolerancias de las piezas impresas

Ensamble de la máquina

Ajustar y lubricar los bujes; rodamientos; guías; etc

### 3.2 Desarrollo del proyecto

En esta sección se describe paso a paso todo el procedimiento que se llevó a cabo

para el diseño de una CNC con el objetivo de mejorar la manufactura de PCBs y reducir

los riesgos de falla.

### 3.2.1 Definición de proyecto

Para comenzar en la realización de este proyecto se pensó en una máquina que diera

solución alguna problemática y se eligieron a los integrantes adecuados para formar

un equipo de alto rendimiento.

### 3.2.2 Elección de proyecto

Ya que hemos definido hacia dónde va el proyecto, se dieron varias propuestas que

se muestran a continuación:

Tabla 3.2 Tabla de propuestas

Nombre | Propuesta
Arzate Valle Jose Martin | Maquina CNC
Flores Figueroa Alejandro | Sistema de llenado y sellado de bolis.

Calibración y configuración de los drivers para los motores paso a paso

Configuración del software de código G

Entrega

Reyes Araujo Aldo | Protección para soldadura de mano.
Roque Morales Alejandro | Sistema de enfriamiento de hielera.
Tzec Vargas Arath | Compuerta automática para perros.

### 3.2.3 Boceto

Para elaborar un boceto del proyecto se tomaron ideas de máquinas CNC que están

a la venta y se muestran en las siguientes figuras.

Figura 3.1 CNC de 3 ejes con guías lineales para trabajos en madera

Figura 3.2 CNC de 3 ejes con bandas

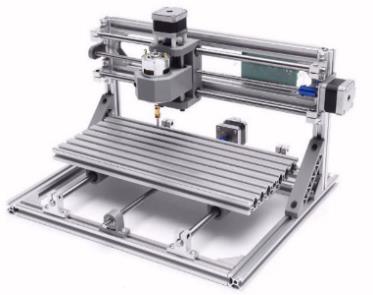
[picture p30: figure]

Figura 3.3 CNC de 3 ejes con guías lineales

### 3.2.4 Presupuesto estimado del proyecto

La tabla 3.3 muestra un presupuesto estimado del proyecto, para proceder a la compra

de los materiales necesarios para el desarrollo del proyecto.

Tabla 3.3 Tabla de presupuesto

Material | Cantidad | Precio Unitario | Total
Motor DC 755 | 1 | $748 | $748
Motor a pasos | 3 | $170 | $510
Rollo de PETG 1.75mm 1KG | 1 | $449 | $449
Fuente de alimentación 24V | 1 | $ 409 | $409
Base soporte para riel eje lineal | 4 | $55 | $220

Rodamiento LM12UU | 8 | $65 | $520
Guía lineal 8mm 300mm | 1 | $110 | $110
Perfil aluminio 2080 500mm | 1 | $650 | $650
Perfil de aluminio 2040 400mm | 2 | $258 | $516
Perfil de aluminio 2020 300mm | 6 | $85 | $510
Guía lineal 12mmX1500mm | 1 | $575 | $575
Guía lineal 10mmX300mm | 1 | $230 | $230
Sensor de velocidad | 1 | $150 | $150
Tabla de madera 240mmX160mm | 1 | $200 | $200
Total | $5,797

### 3.2.5 Investigación de software de calibración de motores

GRBL es un firmware para el control de máquinas CNC, está pensado para usarse en

placas Arduino con un microcontrolador Atmega328, ya que nos permite configurar el

control y desplazamiento de nuestra máquina. Los controladores paso a paso se

clasifican para una longitud de impulso mínima de paso.

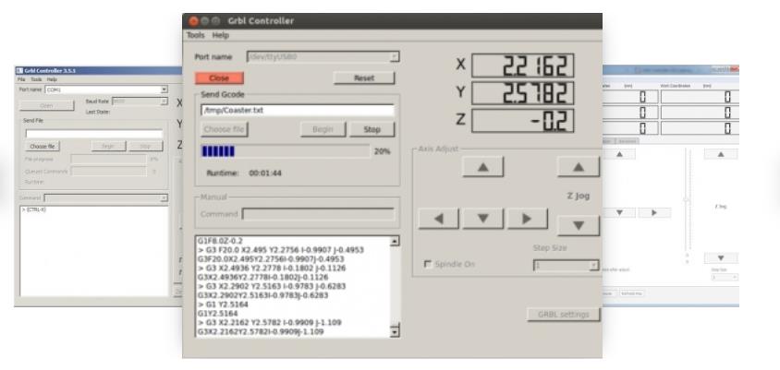
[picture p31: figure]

Figura 3.4 Interfaz del software GRBL

### 3.2.6 Diseño en SolidWorks

Para realizar el proyecto de manera física, primero se requiere un diseño que ayudará

para evitar problemas y proporcionar parámetros para optimizar aspectos cruciales del

proyecto. A continuación, se muestra el diseño en el programa SolidWorks:

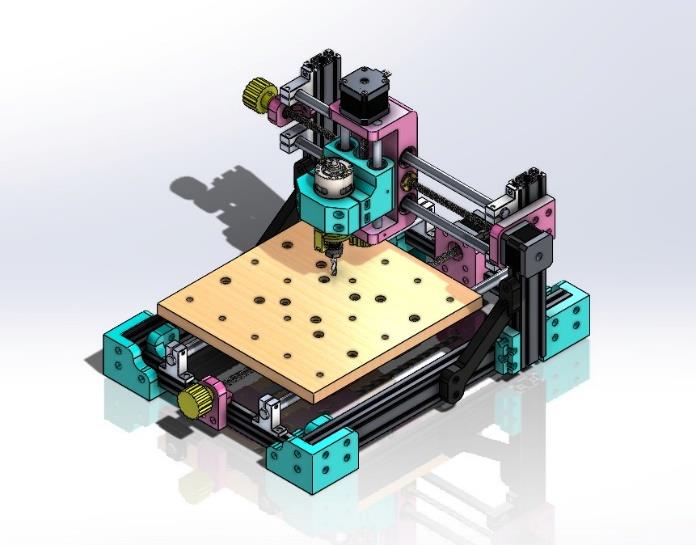
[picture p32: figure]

Figura 3.5 Diseño en SolidWorks

### 3.2.7 Compra de materiales

Se realizó la compra de los materiales listados anteriormente por medio de tiendas en

línea como lo fueron Amazon y Mercado Libre, en la siguiente figura se muestra el

material comprado.

Figura 3.6 Carrito de compras en Mercado Libre

### 3.2.8 Cortar perfiles de aluminio

Se cortaron los perfiles de aluminio en medidas de:

- 40 cm
- 24 cm
- 25.5 cm

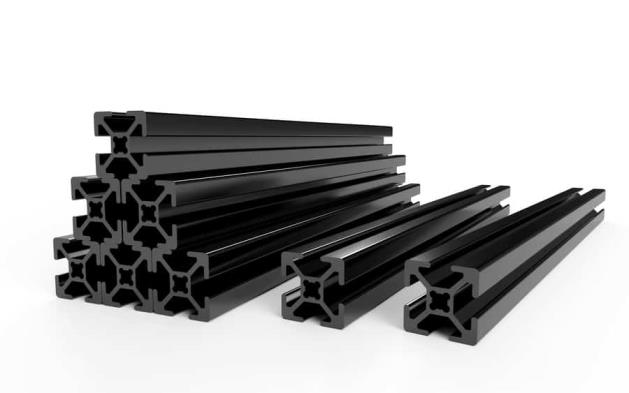
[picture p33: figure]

Figura 3.7 Perfiles de aluminio

### 3.2.9 Impresión de piezas 3D

Las piezas requeridas para el ensamble de la maquina CNC fueron elaboradas en

SolidWorks e impresas en 3D con PETG.

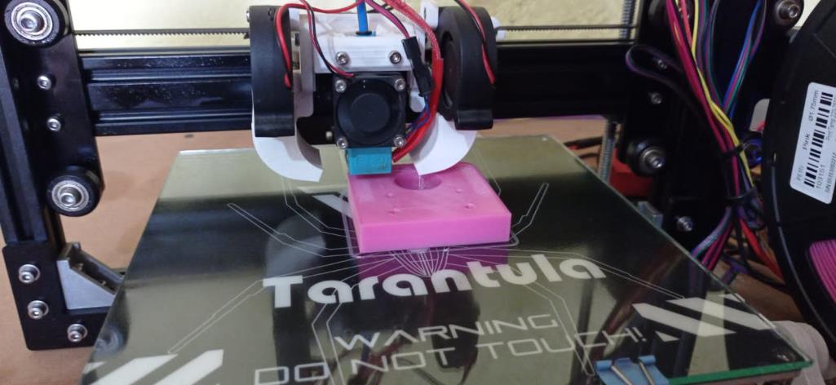
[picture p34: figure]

Figura 3.8 Impresión de piezas

### 3.2.10 Verificar y corregir tolerancias de las piezas impresas

Cuando las piezas son impresas en 3D algunas veces pueden tener un cierto grado

de error, por lo tanto, para arreglar estas tolerancias, es necesario tomar alguna de

estas dos acciones, lijar la pieza o hacer la corrección de este error en el diseño y

volver a imprimir.

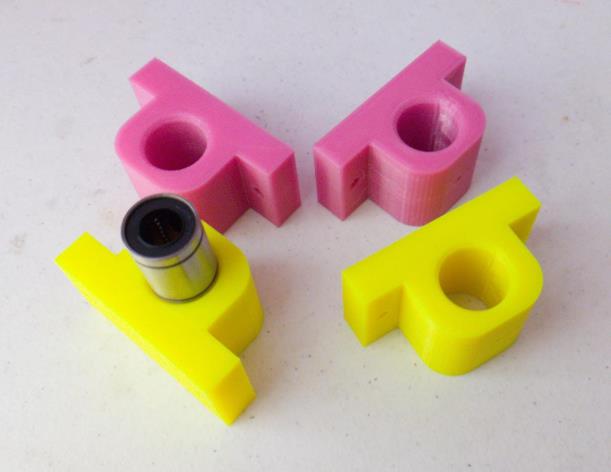
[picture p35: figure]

Figura 3.9 Verificación de tolerancias

### 3.2.11 Ensamble de maquina

Se comenzó con la base que albergara el eje Y como se muestra en la figura 3.10.

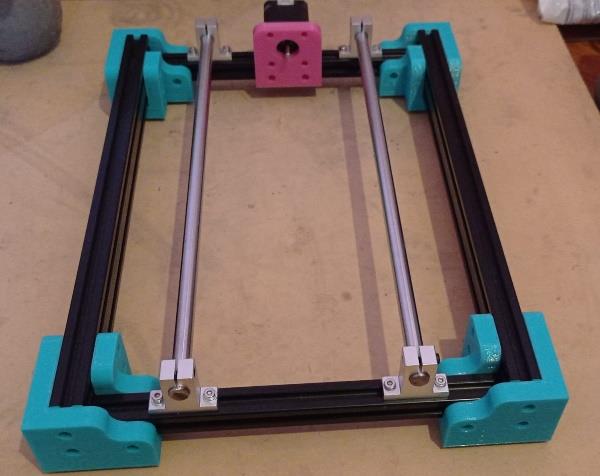
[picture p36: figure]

Figura 3.10 Ensamble eje Y

Posteriormente en la figura 3.11 se muestra montada la tabla a la cual se fijarán las

PCBs para su maquinado.

Figura 3.11 Base de madera montada

En la figura 3.12 se muestran los ejes X y Z colocados para finalmente montar el

soporte del motor que se muestra en la figura 3.13.

Figura 3.12 Montaje ejes X-Z

Figura 3.13 Soporte del motor

3.2.12 Ajustar y lubricar los bujes, rodamientos, guías, etc.

En este proyecto se decidió utilizar dos tipos de lubricación en los componentes

mecánicos del mismo, por un lado, lubricación por aceite y por la otra lubricación por

grasa.

### 3.2.13 Configuración del software de código G

Cnc.js que es una interfaz para el controlador de fresado CNC, la interfaz que este

tiene nos pareció amigable y de un fácil uso para el usuario.

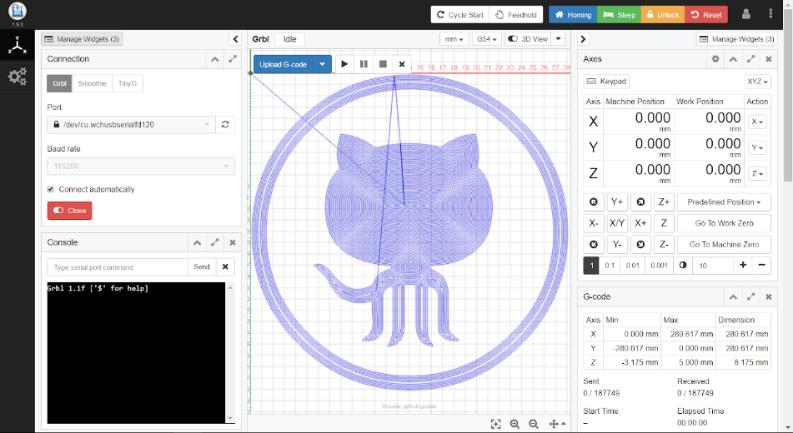
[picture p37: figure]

Figura 3.14 Interfaz Cnc.js

### 3.3 Entrega del proyecto

Se entrega una maquina CNC para la manufactura de PCBs con el fin de reducir el

riesgo de falla, así como su respectivo reporte donde se presenta el desarrollo,

resultado y conclusiones.

## CAPÍTULO 4. RESULTADOS Y CONCLUSIONES

### 4.1 Resultados

En esta sección se describen los resultados obtenidos a lo largo del proceso de diseño

y construcción de la maquina CNC para la mejora en la manufactura de PCBs y

disminuir el riesgo de fallo.

### 4.1.1 Elección de proyecto

Una vez realizadas las propuestas de los integrantes del equipo se procedió a analizar

cada una de estas, por su viabilidad, interés y cantidad de conocimientos aplicados a

dicha propuesta. La propuesta seleccionada fue la maquina CNC de Martín.

### 4.1.2 Boceto

Después de tomar como inspiración algunos de los diseños de máquinas CNC que se

encuentran a la venta en el mercado se realizó el boceto para posteriormente definirlo

en el software de SolidWorks.

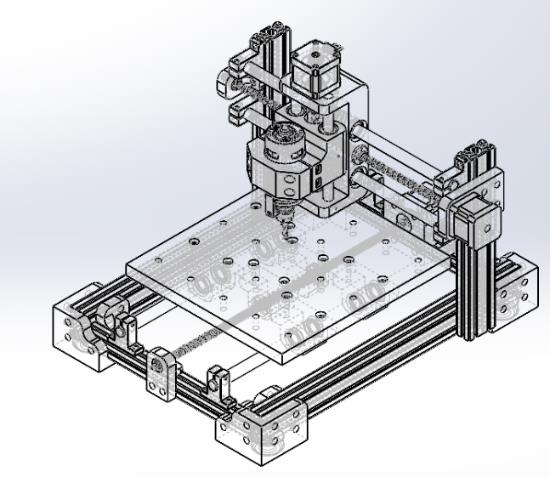
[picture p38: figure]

Figura 4.1 Boceto maquina CNC

### 4.1.3 Presupuesto final del proyecto

La tabla 4.1 muestra el coste final del proyecto, ya que se añadieron materiales que

fueron anexándose durante el desarrollo del proyecto.

Tabla 4.1 Tabla de coste final del proyecto

Material | Cantidad | Precio Unitario | Total
Motor DC 755 | 1 | $748 | $748
Motor a pasos | 3 | $170 | $510
Rollo de PETG 1.75mm 1KG | 1 | $449 | $449
Fuente de alimentación 24V | 1 | $409 | $409
Base soporte para riel eje lineal | 8 | $55 | $440
Rodamiento LM12UU | 8 | $65 | $520
Guía lineal 8mm 300mm | 1 | $110 | $110
Perfil aluminio 2080 500mm | 1 | $650 | $650
Perfil de aluminio 2040 400mm | 2 | $258 | $516
Perfil de aluminio 2020 300mm | 6 | $85 | $510
Guía lineal 12mmX1500mm | 1 | $575 | $575
Guía lineal 10mmX300mm | 1 | $230 | $230
Sensor de velocidad | 1 | $150 | $150
Tabla de madera 240mmX160mm | 1 | $200 | $200
Arduino UNO | 1 | $150 | $150
Kit de tarjeta CNC shield | 1 | $330 | $330
Tornillos cabeza Allen M4x12 | 47 | 1.5 | 70.5
Tornillos cabeza Allen M4x10 | 16 | 1 | 16
Tornillos cabeza Allen M4x20 | 8 | 1.5 | 12
Tornillos cabeza Allen M3x12 | 25 | 1.5 | 37.5
Tornillos cabeza circular o botón Allen M5x30 | 12 | 2 | 24
Tornillos cabeza Allen M5x35 | 4 | 1.5 | 6
Tuercas de seguridad M5 | 12 | 1.5 | 18
Tuercas T M4 | 71 | 6 | 426
$7,107

### 4.1.4 Compra de materiales

En la figura 4.2 se muestra el material adquirido por medio de tiendas digitales.

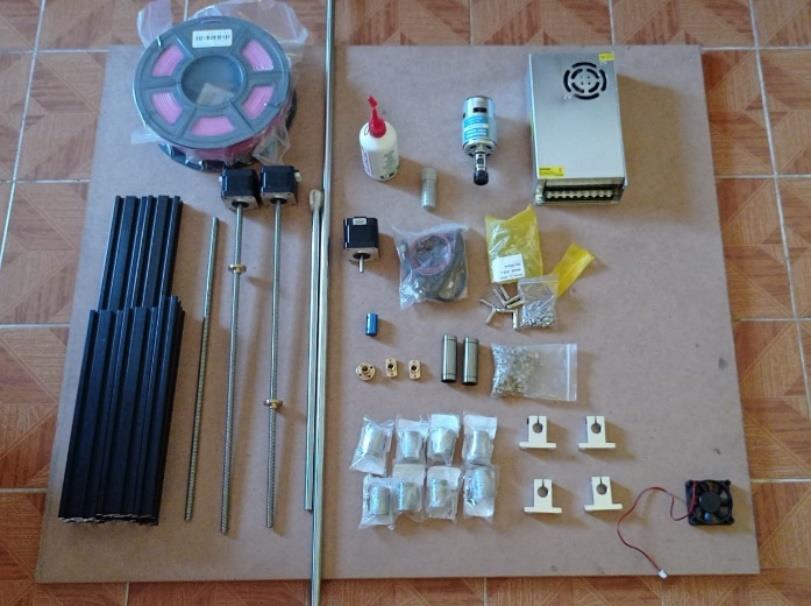
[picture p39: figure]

Figura 4.2 Material adquirido

### 4.1.5 Cortar perfiles de aluminio

Se realizaron los cortes de los perfiles de aluminio en las medidas mencionadas con

anterioridad, el resultado se muestra en la figura 4.2.

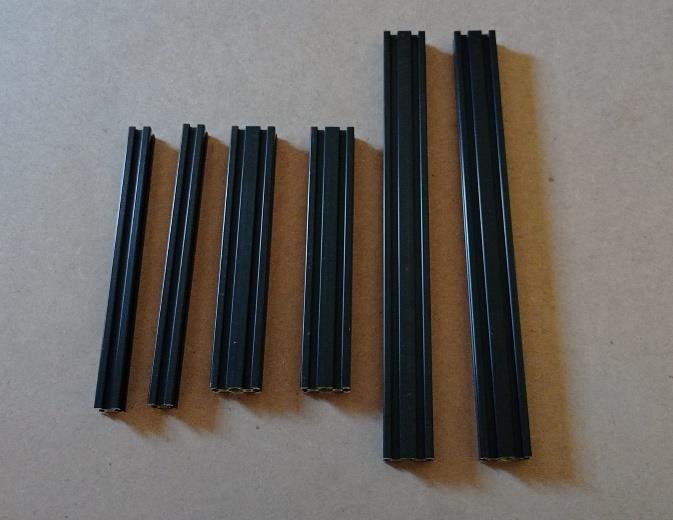
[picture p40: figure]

Figura 4.3 Perfiles de aluminio cortados

### 4.1.6 Impresión de piezas 3D

En la siguiente serie de imágenes se muestran algunas de las piezas impresas en 3D

como lo son los soportes de las esquinas en la base del eje “Y”, el soporte del motor y

los soportes de los husillos.

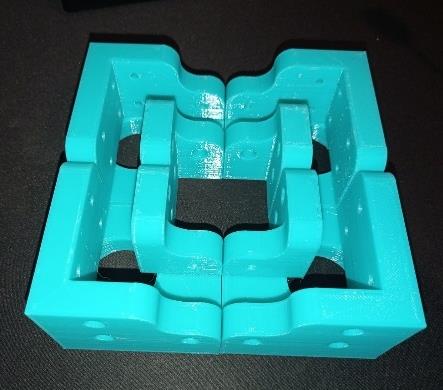
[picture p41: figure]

Figura 4.4 Soportes base eje Y

Figura 4.5 Soporte Motor | Figura 4.6 Soportes de los husillos

### 4.1.7 Corrección de tolerancias

Como se había mencionado antes la corrección de tolerancias había dos opciones,

hacer los ajustes en el diseño de cada una de las piezas o lijar, en este caso se decidió

lijar hasta el punto en que los rodamientos entraran con una ligera presión, los

resultados se muestran en las siguientes figuras.

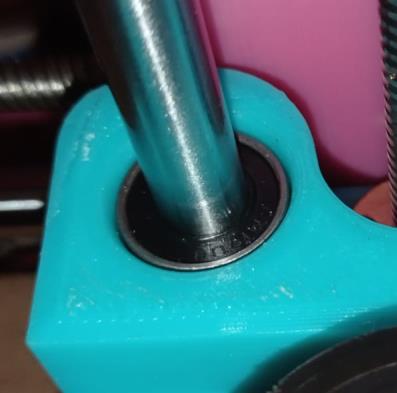
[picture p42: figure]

Figura 4.7 Rodamiento eje Y | Figura 4.8 Rodamiento en eje Z | Figura 4.9 Rodamientos eje X

### 4.1.8 Ensamble de la maquina

En la figura 4.10 se muestra el ensamble final de la maquina CNC, ya lista para realizar

la lubricación en cada uno de los ejes y/o elementos involucrados en algún movimiento.

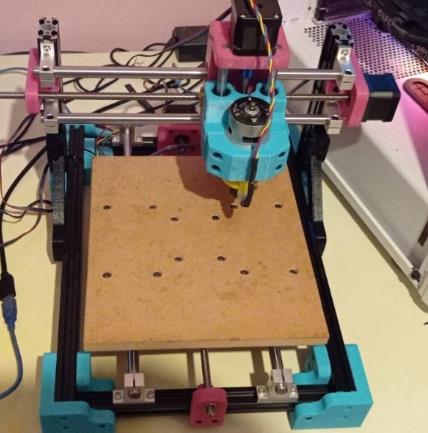
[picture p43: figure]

Figura 4.10 Maquina CNC ensamblada

### 4.1.9 Lubricación de bujes, rodamientos y guías

La lubricación por aceite se destinó para las guías de la CNC, esto pues creemos que

la lubricación por aceite en esas zonas nos ayudará a prevenir el calentamiento ya que

son partes que están trabajando y moviéndose constantemente, además de que ésta

misma naturaleza de trabajo lleva a un desgaste continuo de las partes lo cual la

lubricación por aceite puede ayudar a mitigar, además de que los elementos rodantes

son algo pequeños por lo cual nos vemos beneficiados al usar aceite pues estas zonas

son más accesibles mediante la lubricación por aceite.

Figura 4.11 Lubricación eje Z | Figura 4.12 Lubricación eje X

En el caso de la grasa se eligió para los husillos, pues ayuda mucha a asegurar el

buen funcionamiento de las piezas móviles de este tipo además de que nos puede

ayudar a asegurar a dispersar algo del calor con el que se verá enfrentado este

elemento de la CNC, además de que la grasa se mantendrá en su lugar una cantidad

de tiempo mayor.

### 4.1.10 Configuración de los drivers para motores paso a paso

Cálculos

Primeramente, se necesita calcular el voltaje que se necesitará para calibrar a los

drivers de los motores, para esto se han utilizado las siguientes ecuaciones. La razón

de esta ecuación es que se está tomando un motor que funciona con 1.5A al que se

desea operar al 80% de su funcionamiento.

max = 1.5 ∗ 0.8 < = > Imax = 1.2A

La siguiente fórmula es la fórmula general para calcular el voltaje necesario según el

motor que se tiene.
Vref = Imax 0.8 Rs

Se toma como dato que se tendrá un valor de .1 Ω además de que se reemplazará Imax

según el dato antes obtenido, después de sustituir estos datos dentro de la ecuación

original podremos tener el voltaje que buscamos.

Vref = 1.2A ∗ 8 ∗ 0.1 < = > Vref = 0.96v

Procedimiento en el driver físico.

Se identificó en lugar se encontraba la tierra del driver, esto encontrando la parte que

indica 5V/GND.

Figura 4.13 Identificación de alimentación en el driver

Posteriormente una vez identificada la tierra se utilizó un jumper para conectarlo a la

punta positiva del multímetro, esto nos permitirá visualizar en el multímetro el voltaje

que necesitaremos para calibrar al driver

Figura 4.14 Visualización de voltaje necesario para calibración

Una vez teniendo la habilidad de visualizar el voltaje lo que sigue es ajustar el

potenciómetro del driver hasta llevarlo al valor deseado, se necesita de mantener las

vueltas del potenciómetro con sutileza para lograr una mayor precisión y obtener el

valor deseado o una lo suficientemente cercano.

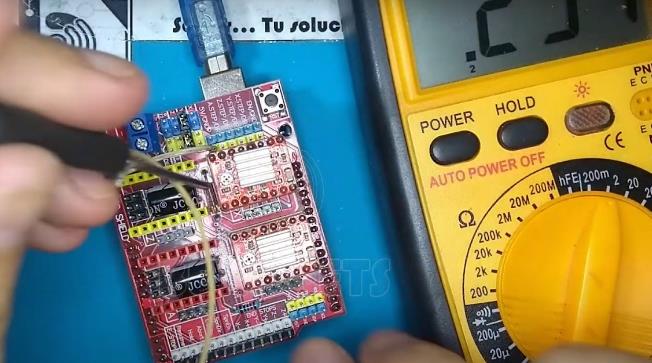
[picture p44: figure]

Figura 4.15 Ajuste de resistencia

Una vez que se han calibrado los drivers se procede a conectar los dos motores a

pasos en sus pines correspondientes, un motor servirá para moverse a lo largo del eje

X y el segundo en el eje Y.

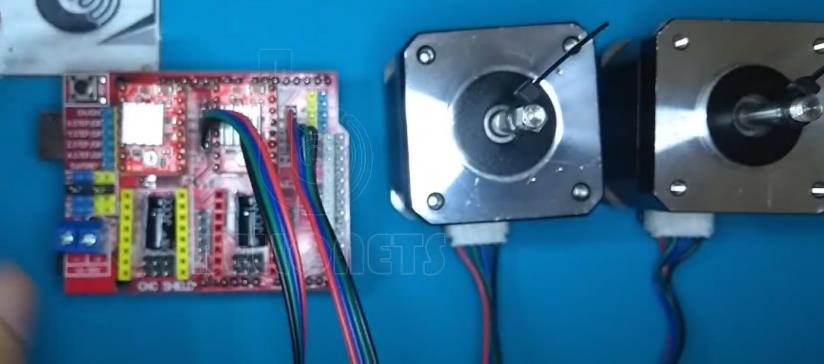
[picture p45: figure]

Figura 4.16 Conexión de motores al driver

Una vez conectados ambos motores lo que resta por hacer es conectar el driver a una

fuente y voltaje y posteriormente conectarlo a una PC para llevar a cabo las pruebas

de funcionamiento según el programa deseado.

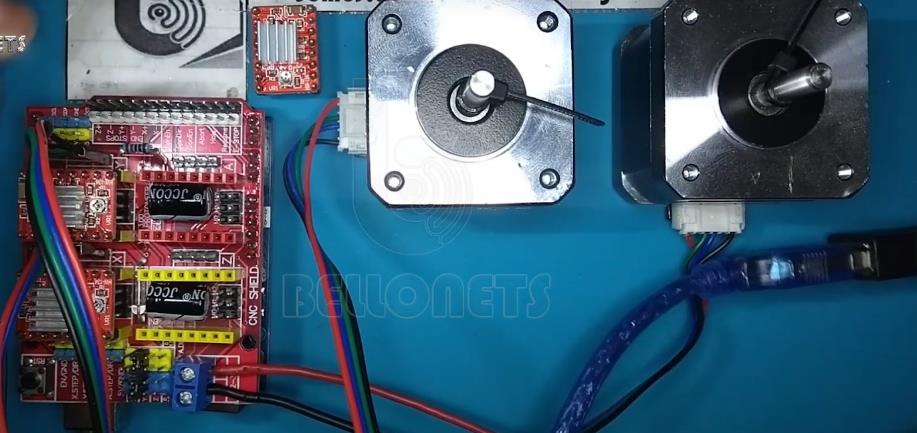
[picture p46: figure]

Figura 4.17 Pruebas a los motores

### 4.1.11 Configuración de parámetros para el driver CNC -GRBL

Se configuró los drivers a 1/8 de paso y los husillos del x y y tienen un paso de 8mm

por vuelta Y el del eje z 2 mm por vuelta. En la siguiente imagen se muestran los drivers

para los motores en nuestro caso se colocaron jumpers en M0 y M1, es por ello que

se configuró a ⅛.

Figura 4.18 Driver empleado

En la siguiente tabla se muestran los datos sobre la configuración de los pasos al

nosotros tener configurado los drivers en ⅛ necesitaremos de 8 veces la cantidad de

pasos para poder cubrir una distancia.

Tabla 4.2 Tabla de configuración de pasos

A4988

| MS1 JUMPER | MS2 JUMPER | MS3 JUMPER
Single Step | 0 | 0 | 0
1/2 Step | 1 | 0 | 0
1/4 Step | 0 | 1 | 0
1/8 Step | 1 | 1 | 0
1/16 Step | 1 | 1 | 1

El driver GRBL necesita una configuración previa para funcionar y tener la mejor

precisión posible, para esto se configurarán los parámetros del $0 -$22, cabe

mencionar que algunos parámetros se colocaron de default.

Dependiendo del motor a pasos que se compró, se buscó el datasheet para visualizar

los grados por paso que da el motor, este motor cuenta con 1.8°, pero necesitamos

saber cuántos pasos requiere para dar una vuelta, por lo tanto, se tiene lo siguiente:

360°(Un giro completo)
1.8° | = Se requieren 200 pasos para una vuelta completa

Lo que sigue después es saber dependiendo de la varilla, cuantos milímetros se

recorre por cada vuelta, por lo tanto, para las varillas que se compraron se tiene que

por cada vuelta recorre 8 milímetros, con estos datos sabemos que necesitamos 200

pasos para cubrir una distancia, pero al estar configurado en ⅛ esto quiere decir que

necesitaremos 8 veces esa cantidad de pasos, por lo que se hace una multiplicación:

200 pasos*8=1600

Esta cantidad de pasos será dividida entre la cantidad de mm que tiene de avance por

vuelta la varilla que será utilizada en el proyecto, en nuestro caso el avance es de 8mm

por vuelta, por lo tanto:
1600
8

= 200 pasos

De esta manera se colocan los parámetros del $100 al $101 que corresponden a los

pasos por milímetros de los motores x, y; para el caso del motor z el dato cambia pues

en este se recorren 2 mm en lugar de 8 por lo tanto:

200 pasos*8=1600
1600
2

= 800 pasos

Después configurar el ancho de pulso que manda el Arduino, se colocó en 10.

Se colocaron los valores de los pasos en los diferentes valores según los datos que se

habían calculado.

Figura 4.19 Valor de los pasos

Los puntos del 110 al 112 por otro lado son los datos que nosotros indicamos como la

velocidad máxima a la que nosotros configuramos a los motores para alcanzar como

una condición fija.

Figura 4.20 Velocidad por eje

Los datos del 120 al 122 muestran los datos de aceleración que nosotros designamos

a los motores y también el límite de aceleración que estos tienen. Se configuró a 999

para desactivar la aceleración.

Figura 4.21 Aceleración por eje

En el caso de los datos del 130 al 132 son los parámetros que nosotros establecimos

como la distancia máxima a la que el motor va a viajar es decir la delimitación que

nosotros le estamos otorgando para desplazar.

Figura 4.22 Distancias máximas

La lista de configuraciones queda de la siguiente manera:

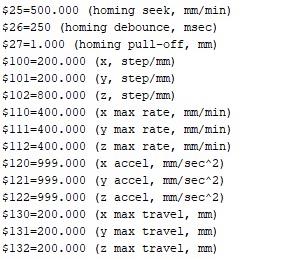
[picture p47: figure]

Figura 4.23 Lista de configuraciones

### 4.1.12 Prueba de funcionamiento

En la primera prueba se volvieron a ajustar los motores, debido a que no estaban bien

calibrados. También se agregó más grasa blanca con litio para que los husillos

funcionaran de una mejor manera, ya con esta grasa los ejes se pudieron mover

correctamente. De la misma manera al hacer estos cambios la maquina funciono

mejor.

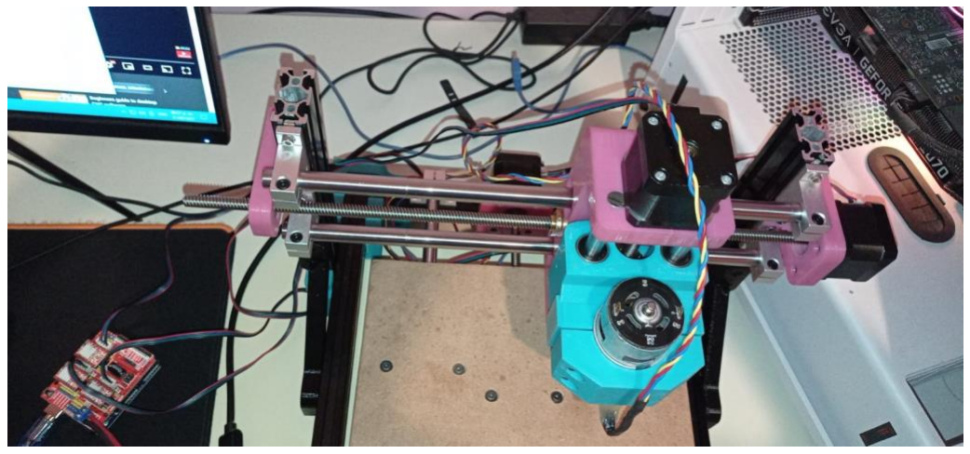
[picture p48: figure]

Figura 4.24 Prueba de funcionamiento

### 4.2 Conclusiones y Recomendaciones

Conclusiones

Durante la elaboración de este proyecto se obtuvieron varias nuevas perspectivas

sobre la importancia del desarrollo bien estructurado de un proyecto de este tipo, la

investigación, la planeación, y la administracion del tiempo fueron factores que este

equipo tuvo la oportunidad de manejar de la mejor manera posible haciendo lo posible

para sacar hacia adelante este trabajo; es por esto que hemos entendido el rol tan

importante que varios de estos elementos tienen dentro del desarrollo de un proyecto,

ya sea de indole educativa o dentro de una industria en el futuro.

Además de que se ha aprendido a comprender que cada parte de la máquina que está

siendo desarrollada debe ser fuertemente investigada para poder avanzar

correctamente dentro del desarrollo progresivo de la CNC, desde la elaboracion y

impresion de las diferentes piezas que compondran la maquina hasta el codigo que

nos permitirá controlar las acciones de la máquina, todos estos elementos deben ser

comprendidos para poder ser desarrollados.

Recomendaciones

Este equipo sugiere a cualquiera que desee utilizar este proyecto lea de manera

detenida lo que esté dentro de este documento para poder entender el funcionamiento

de la cnc y sus diferentes elementos, ya sea para poder mejorar este equipo o darle

un uso adecuado, estas características deben de ser tomadas en cuenta para evitar

problemas ya sean fallas de funcionamiento o provocadas por un mal manejo del

equipo.

## REFERENCIAS

C. (2020, 30 diciembre). Qué es el CNC y cómo funciona. Boyfre. Recuperado 12 de

junio de 2022, de https://www.boyfre.com/que-es-el-cnc-y-como-funciona/

Transfer Multisort Elektronik. (2020, 8 septiembre). Motor paso a paso – tipos y

ejemplos del uso de motores paso a paso. Distribuidor de componentes

electrónicos. Tienda en línea: Transfer Multisort Elektronik. Recuperado 12 de

junio | de | 2022, | de | https://www.tme.com/mx/es/news/library-

articles/page/41861/Motor-paso-a-paso-tipos-y-ejemplos-del-uso-de-

motores-paso-a-paso/ (https://www.tme.com/mx/es/news/library-articles/page/41861/Motor-paso-a-paso-tipos-y-ejemplos-del-uso-de-motores-paso-a-paso/)

¿Qué es un Rodamiento? | Tipos | Componentes de un rodamiento | Aplicaciones.

(2020, 12 mayo). NSK. Recuperado 12 de junio de 2022, de

https://www.nskamericas.com/es/services/what-s-a-bearing.html

Valverde, A. (s. f.). ¿Cómo seleccionar el acople ideal para su aplicación? Elvatron.

Recuperado 12 de junio de 2022, de https://www1.elvatron.com/transmicion-

potencia/c%C3%B3mo-seleccionar-el-acople-ideal-para-su-aplicaci%C3%B3n (https://www1.elvatron.com/transmicion-potencia/c%C3%B3mo-seleccionar-el-acople-ideal-para-su-aplicaci%C3%B3n)

Sensor Infrarrojo SMD QRE1113. (s. f.). Naylamp Mechatronics - Perú. Recuperado 12

de | junio | de | 2022, | de | https://naylampmechatronics.com/sensores-

proximidad/351-sensor-infrarrojo-smd-qre1113.html (https://naylampmechatronics.com/sensores-proximidad/351-sensor-infrarrojo-smd-qre1113.html)

Fernández, Y. (2020, 3 agosto). Qué es Arduino, cómo funciona y qué puedes hacer

con | uno. | Xataka. | Recuperado | 12 | de | junio | de | 2022, | de

https://www.xataka.com/basics/que-arduino-como-funciona-que-puedes-

hacer-uno (https://www.xataka.com/basics/que-arduino-como-funciona-que-puedes-hacer-uno)

García, V. (2020, 5 marzo). DESCRIPCIÓN DEL DRIVER A4988 – Electrónica

Práctica Aplicada. ELECTRÓNICA PRÁCTICA APLICADA. Recuperado 13 de

junio de 2022, de https://www.diarioelectronicohoy.com/blog/descripcion-del-

driver-a4988 (https://www.diarioelectronicohoy.com/blog/descripcion-del-driver-a4988)

Filamento PETG - aprenda todo sobre el material PETG para la impresión en 3D. (s.

f.). | Tractus3D. | Recuperado | 13 | de | junio | de | 2022, | de

https://tractus3d.com/es/materials/petg/

Salazar, S. (2017, 30 octubre). ☑ ☑ Husillo, el tornillo sin fin. Sebastián Salazar.

Recuperado 14 de junio de 2022, de https://sebastiansalazar.com/husillo-el-

tornillo-sin-fin/

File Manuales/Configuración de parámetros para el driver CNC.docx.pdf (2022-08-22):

Configuración de parámetros para el driver CNC -GRBL

Se configuró los driver a 1/8 de paso y los husillos del x y y tienen un paso de 8mm por vuelta Y el del eje z 2mm por vuelta.

En la siguiente imagen se muestran los driver para los motores en nuestro caso se colocaron jumpers en M0 y M1, es por ello que se configuro a ⅛.

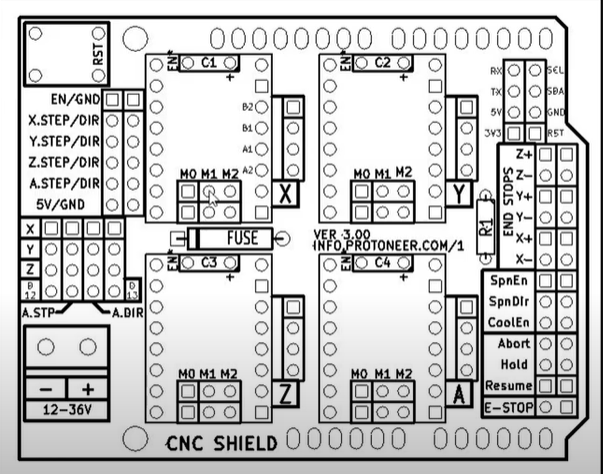
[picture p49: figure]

En la siguiente tabla se muestra los datos sobre la configuracion de los pasos al nosotros tener congifurado los driver en ⅛ necesitaremos de 8 veces la cantidad de pasos para poder cubrir una distancia.

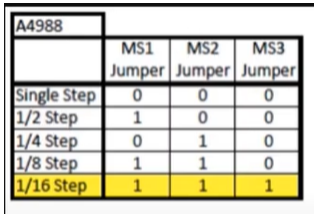
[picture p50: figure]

El driver GRBL necesita una configuración previa para funcionar y tener la mejor precisión posible, para esto se configurarán los parámetros del $0 -$22, cabe mencionar que algunos parámetros se colocaron de default.

Dependiendo del motor a pasos que se compró, se buscó el datasheet para visualizar los grados por paso que da el motor, este motor cuenta con 1.8°, pero necesitamos saber cuantos pasos requiere para dar una vuelta, por lo tanto, se tiene lo siguiente:

(un giro completo)360
1.8 | = Se requieren de 200 pasos para una vuelta completa

Lo que sigue después es saber dependiendo de la varilla, cuantos milímetros se recorre por cada vuelta, por lo tanto, para las varillas que se compraron se tiene que por cada vuelta recorre 8 milímetros, con estos datos sabemos que necesitamos 200 pasos para cubrir una distancia pero al estar configurado en ⅛ esto quiere decir que necesitaremos 8 veces esa cantida de pasos, por lo que se hace una multiplicacion:

200 pasos*8=1600

Ésta cantidad de pasos sera dividida entre la cantida de mm que tiene de avnce por vuelta la varilla que sera utilizada en el proyecto, en nuestro caso el avence es de 8mm por vuelta, por lo tanto:

1600
8 = 200 pasos.

De esta manera se colocan los parámetros del $100 al $101 que corresponden a los pasos por milímetros de los motores x, y ; para el caso del motor z el dato cambia pues en este se recorren 2 mm en lugar de 8 por lo tanto:

200 pasos*8=1600

1600
2 = 800 pasos.

Después configurar el ancho de pulso que manda el Arduino, se colocó en 10

Se colocaron los valores de los pasos en los diferentes valores segun los datos que se habian calculado

Los puntos del 110 al 112 por otro lado son los datos que nosostros indicamos como la velocidad maxima a la que nosotros configuramos a los motores para alcanzar como una condición fija.

Los datos del 120 al 122 muestran los datos de aceleración que nosotros designamos a los motores y también el límite de aceleración que estos tienen. Se configuró a 999 para desactivar la aceleración.

En el caso de los datos del 130 al 132son los parametros que nosotros establecimos como la distancia máxima a la que el motor va a viajar es decir la delimitacion que nosotros le estamos otorgando para desplazar.

La lista de configuraciones queda de la siguiente manera:

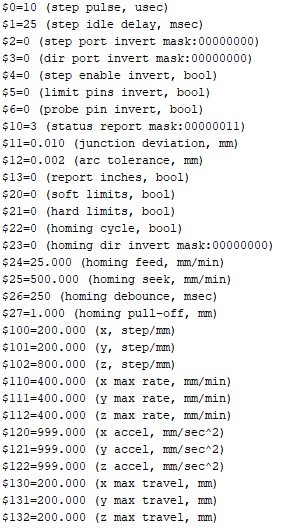
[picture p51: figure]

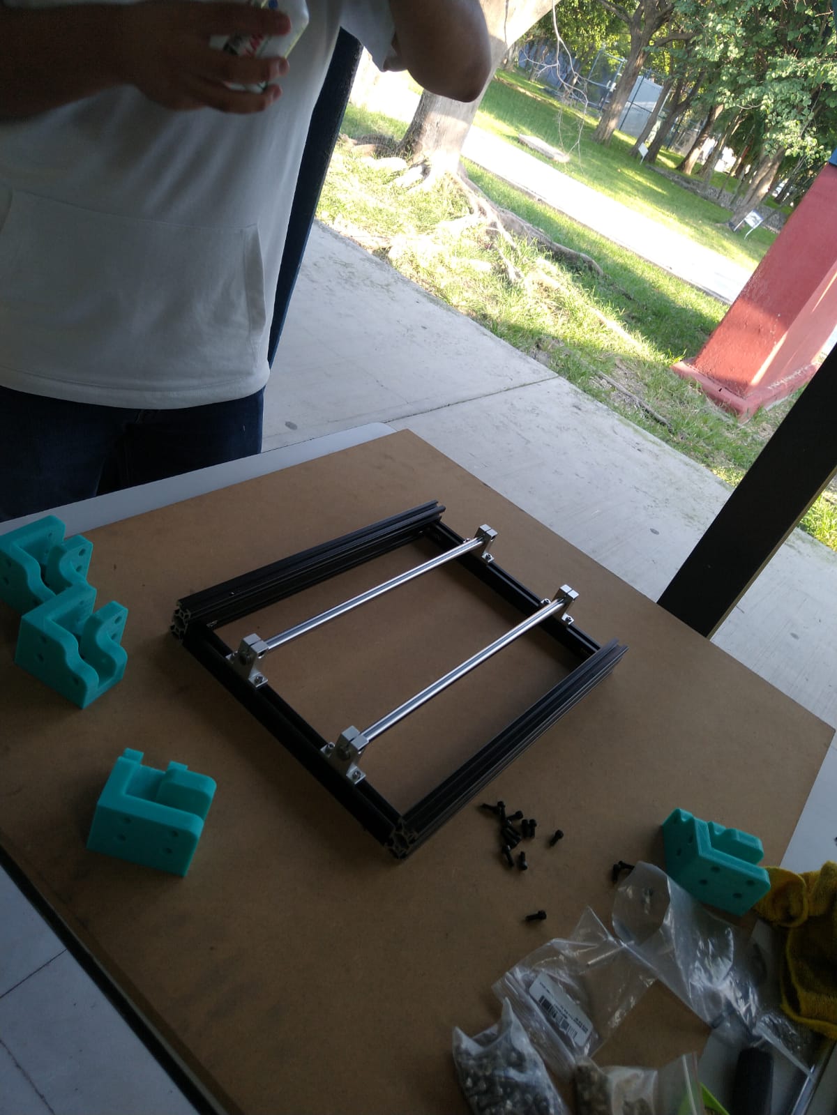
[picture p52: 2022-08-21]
Imagenes/Ensamble De la CNC/Base maquina CNC.jpeg

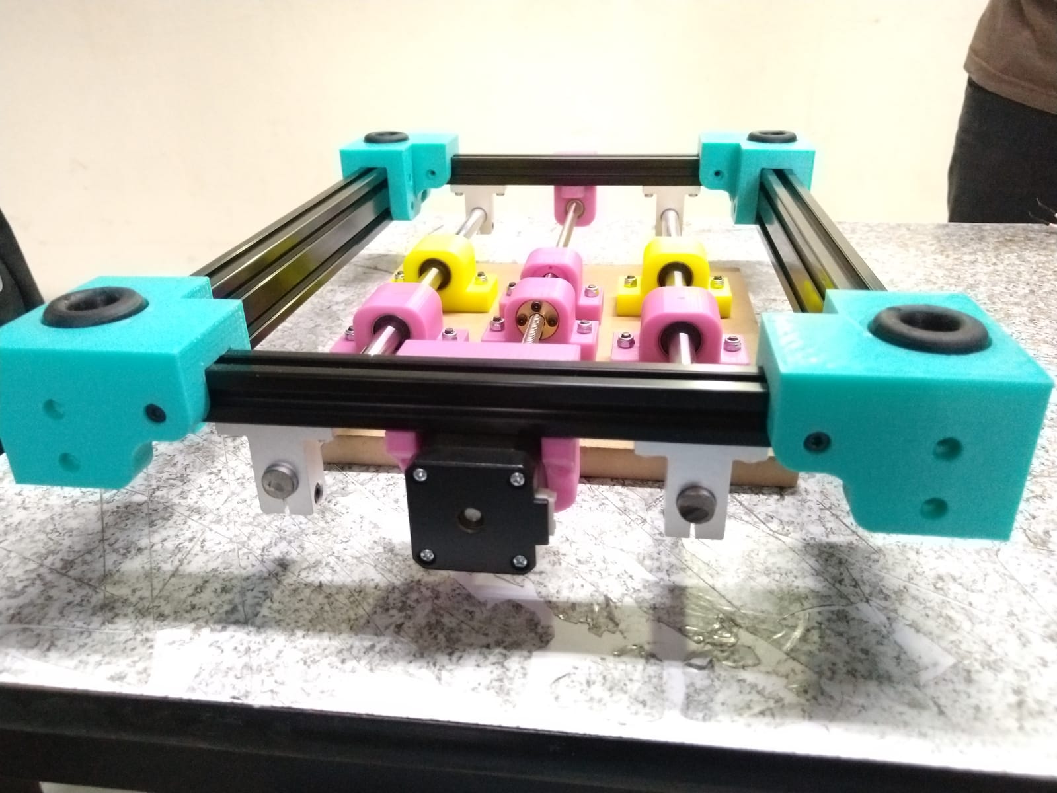
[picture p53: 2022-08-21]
Imagenes/Ensamble De la CNC/Colocacion de cojinetes en el area de trabajo .jpeg

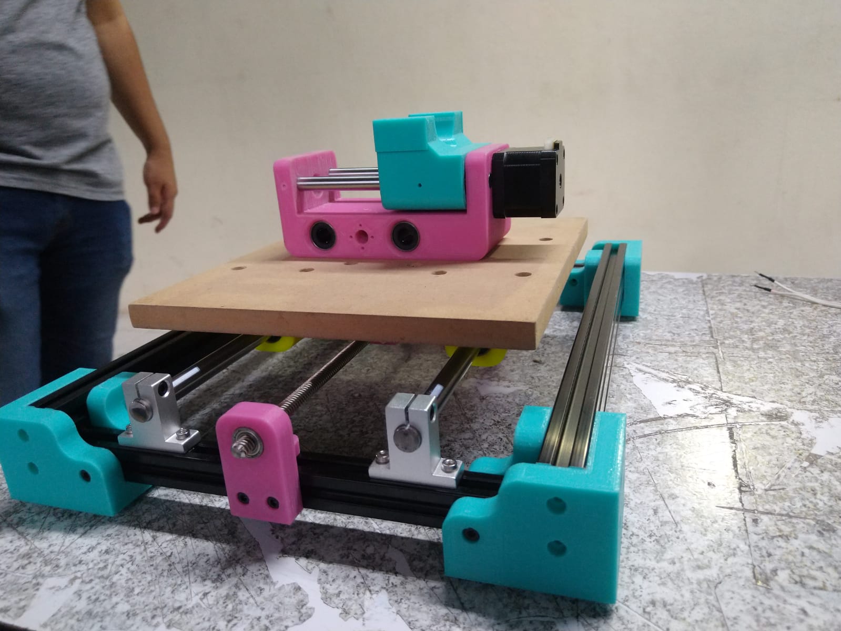
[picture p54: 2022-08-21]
Imagenes/Ensamble De la CNC/Soporte para motor.jpeg

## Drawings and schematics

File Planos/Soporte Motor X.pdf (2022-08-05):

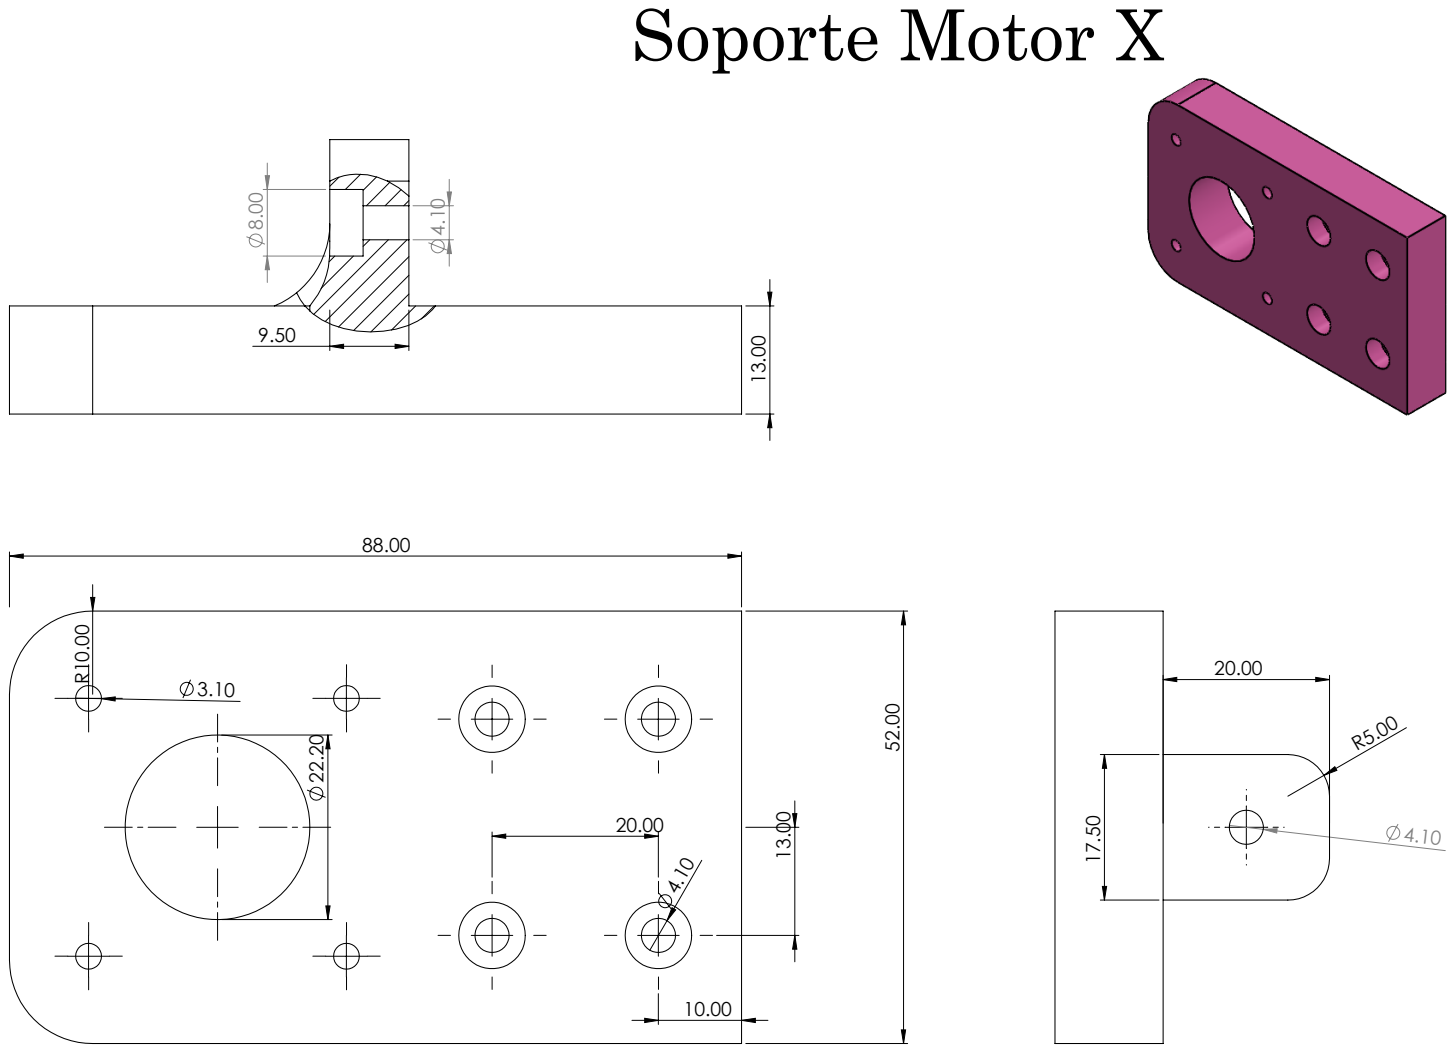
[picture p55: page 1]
Soporte Motor X

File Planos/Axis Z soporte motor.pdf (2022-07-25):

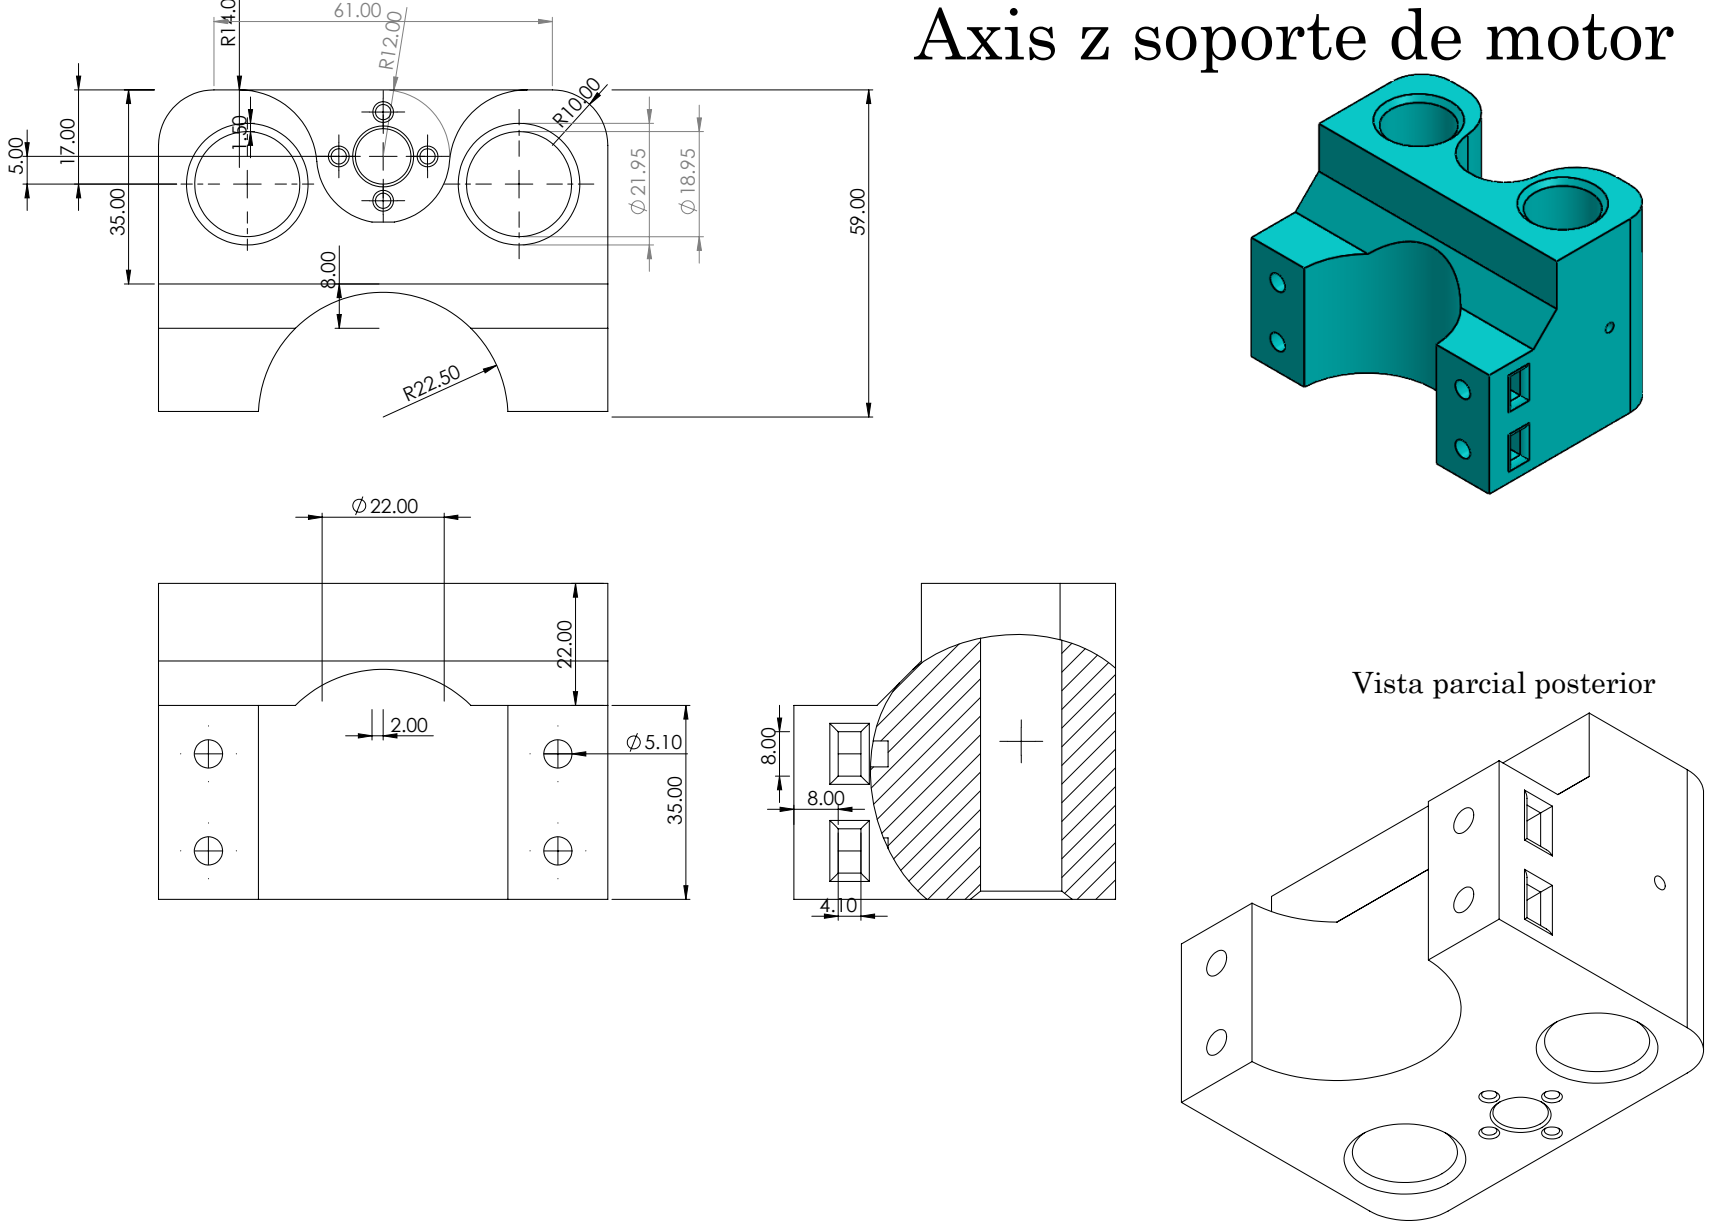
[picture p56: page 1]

Axis z soporte de motor

Vista parcial posterior

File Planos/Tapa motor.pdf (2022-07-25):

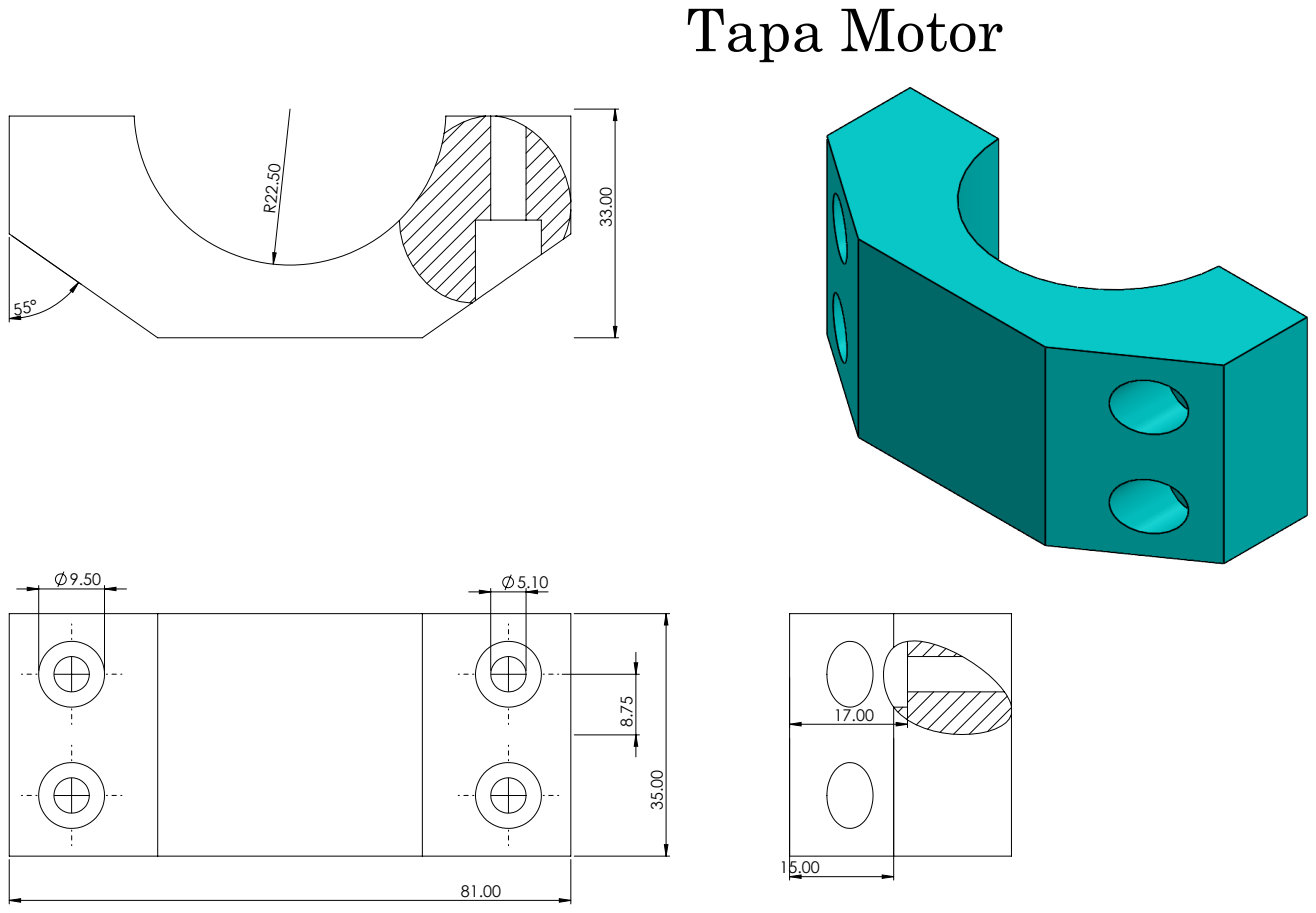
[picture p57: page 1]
Tapa Motor

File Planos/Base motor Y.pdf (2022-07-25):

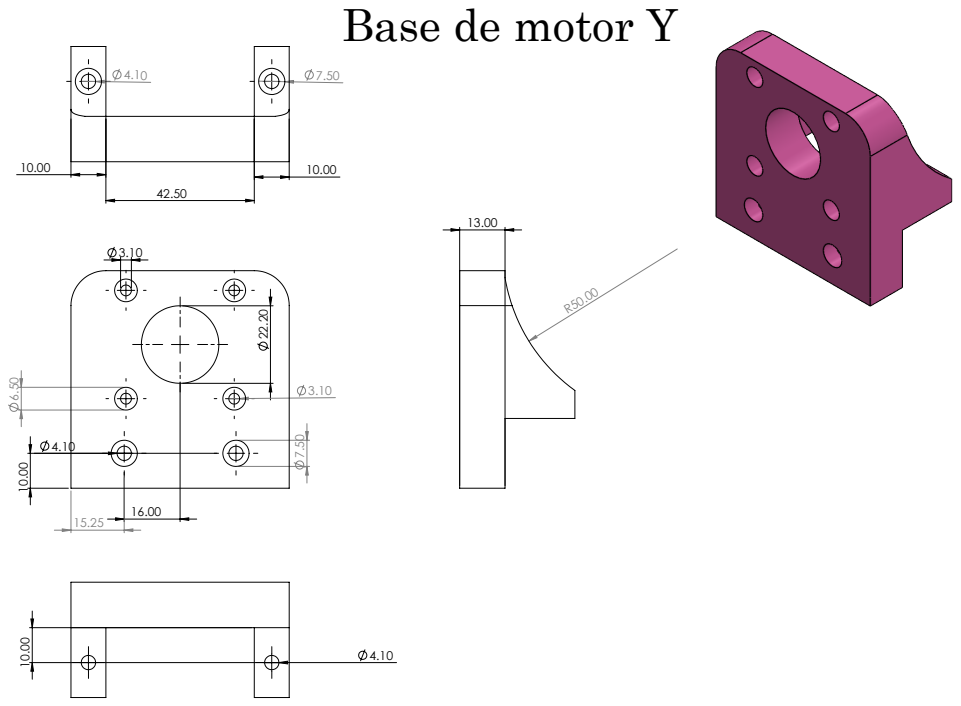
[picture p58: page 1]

Base de motor Y

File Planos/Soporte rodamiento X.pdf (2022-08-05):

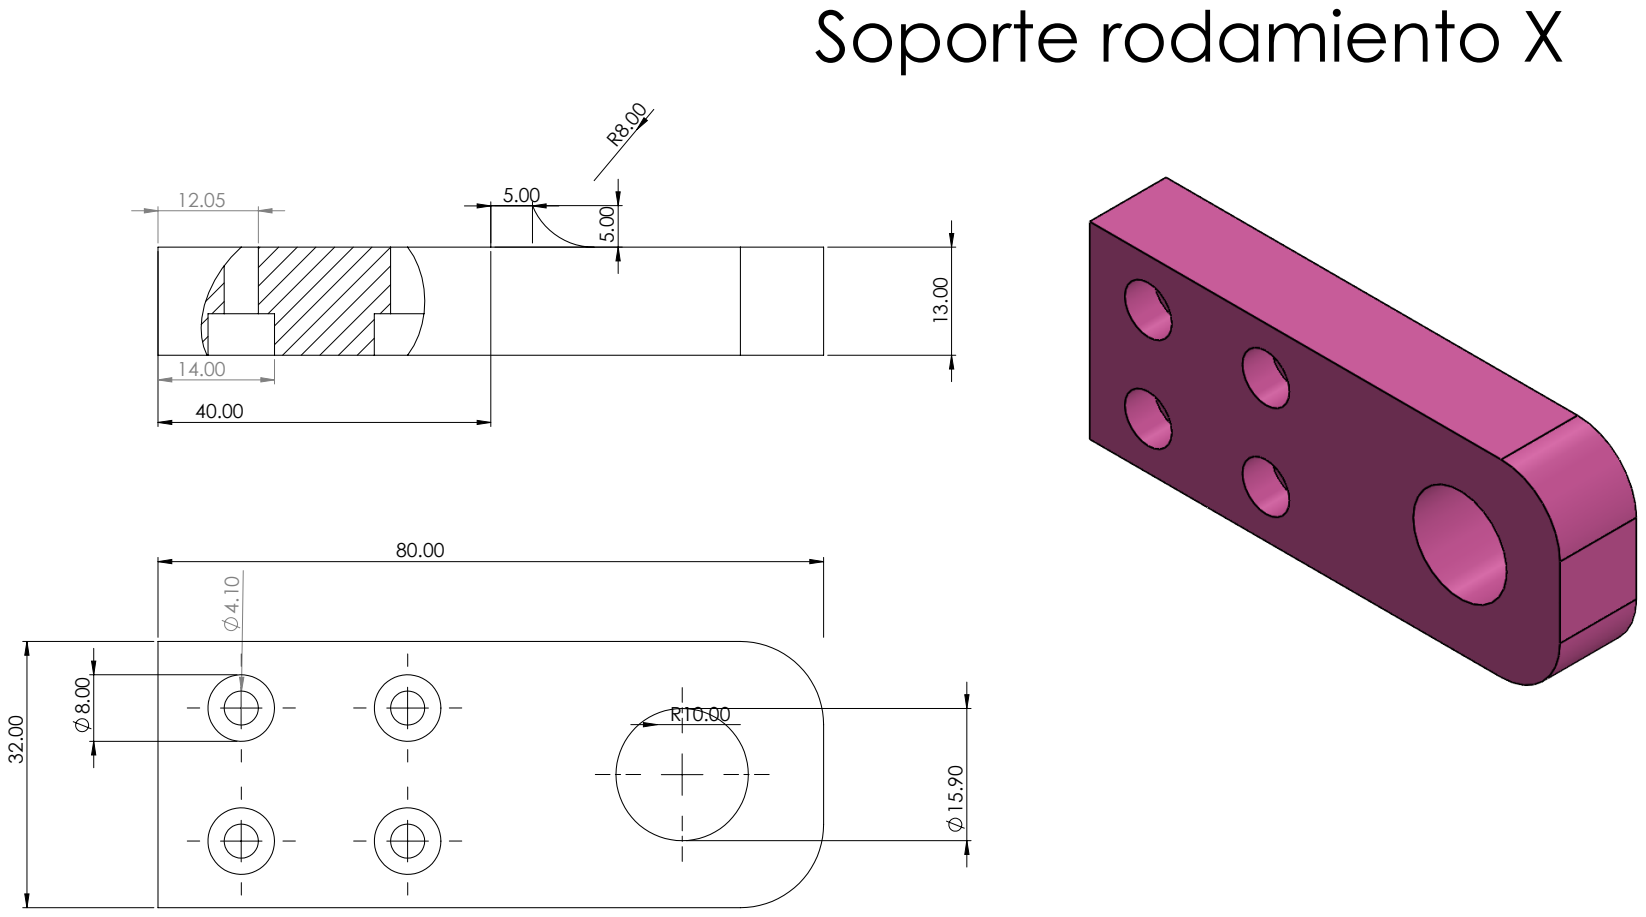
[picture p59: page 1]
Soporte rodamiento X

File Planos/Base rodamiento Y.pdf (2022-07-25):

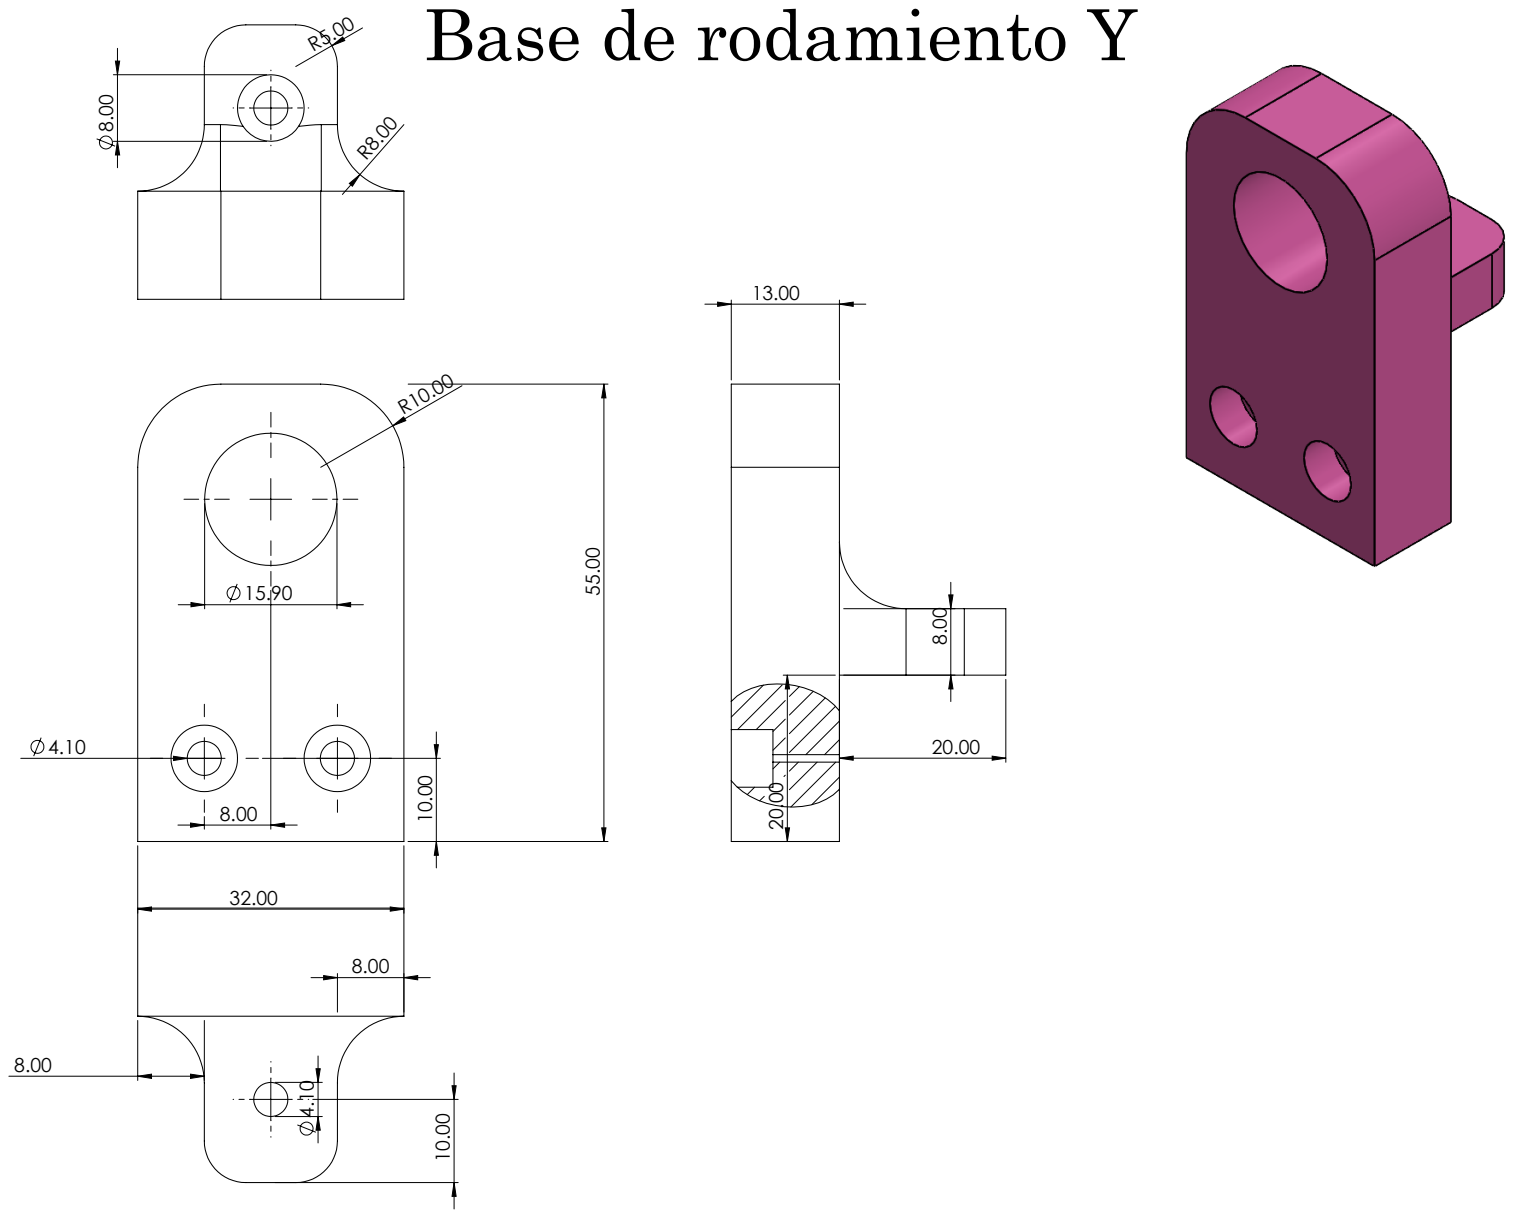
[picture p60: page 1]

Base de rodamiento Y

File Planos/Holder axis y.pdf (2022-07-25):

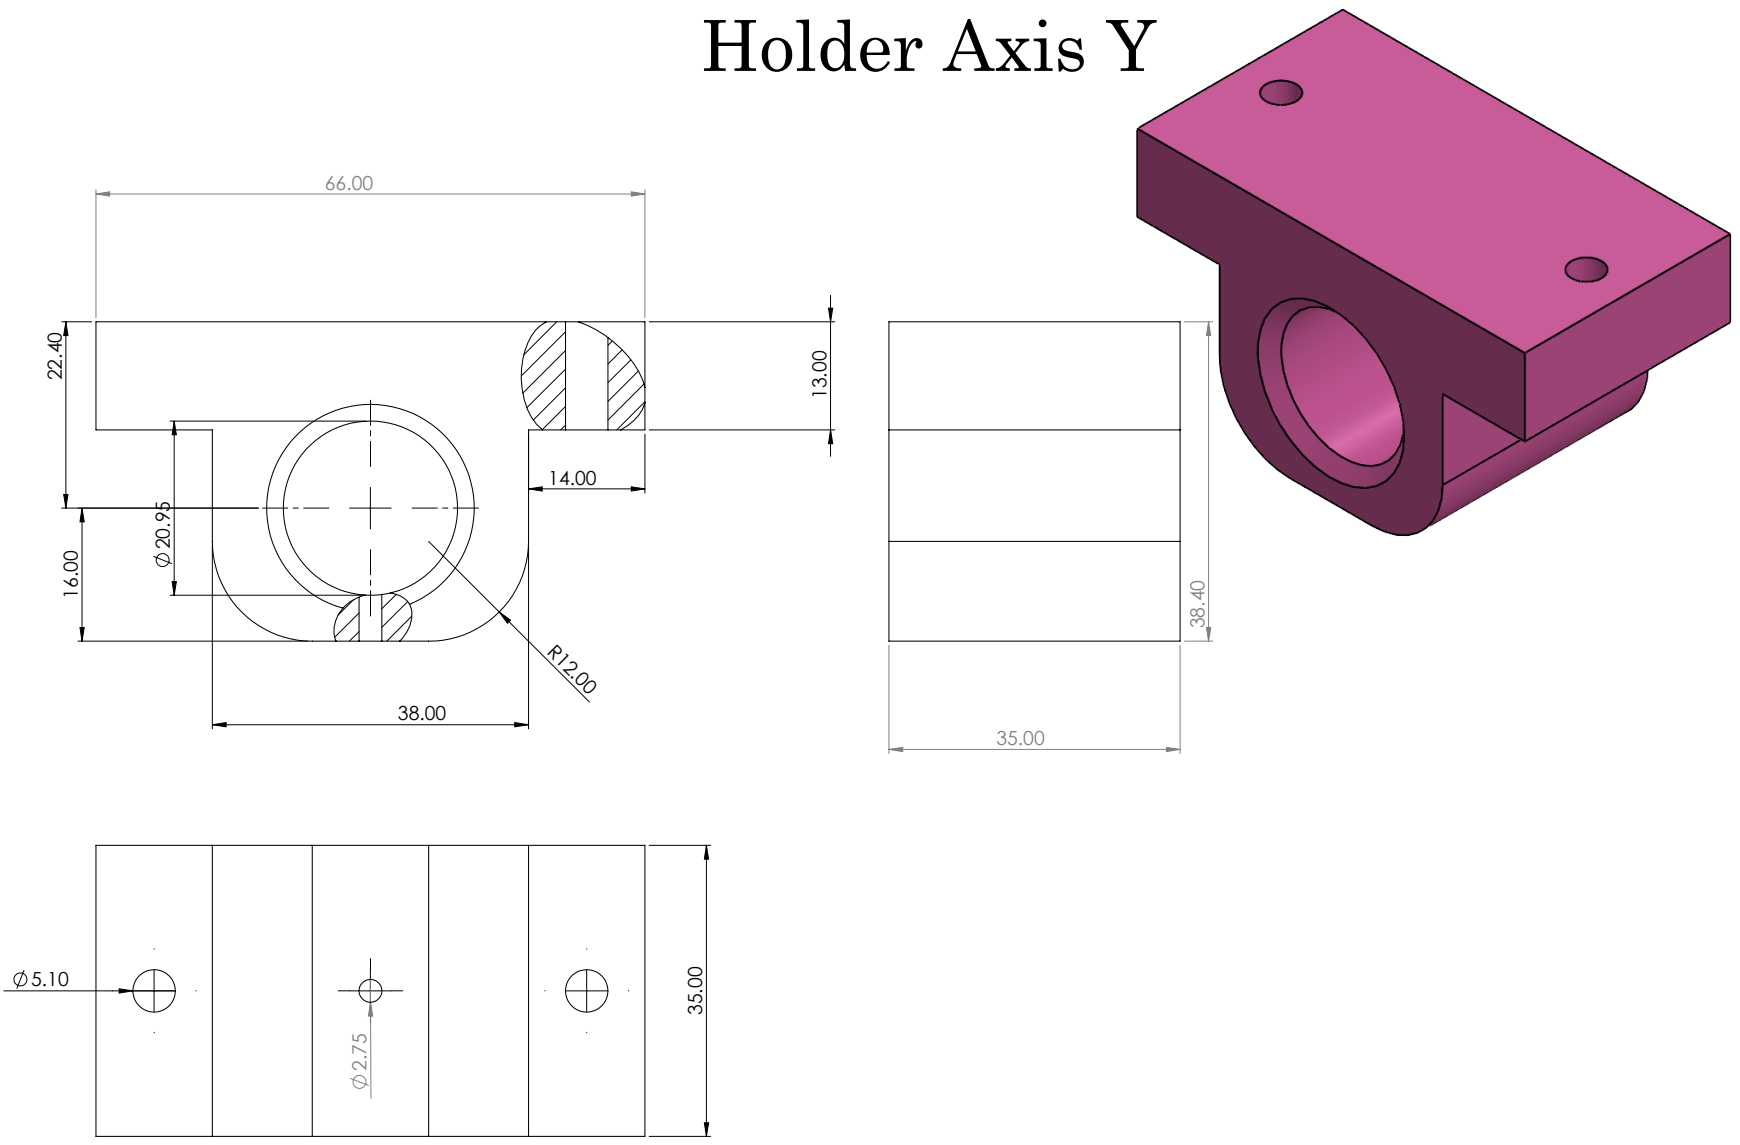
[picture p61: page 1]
Holder Axis Y

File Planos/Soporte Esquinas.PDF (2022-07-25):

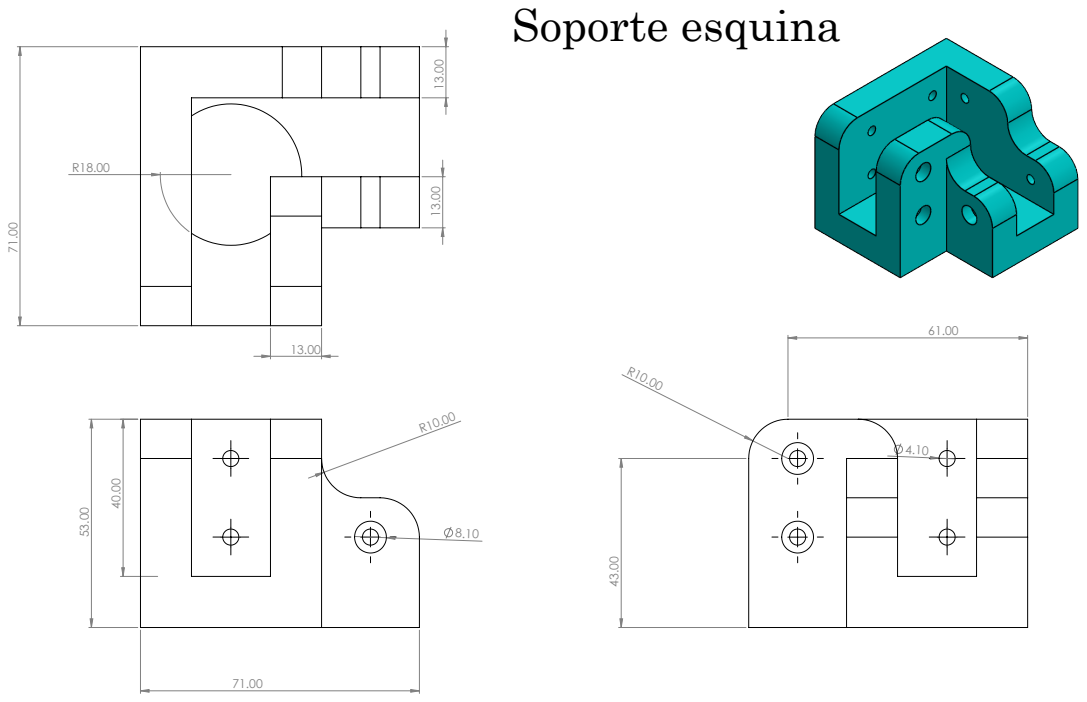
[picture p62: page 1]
Soporte esquina

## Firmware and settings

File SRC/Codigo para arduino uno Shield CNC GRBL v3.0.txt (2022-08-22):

/*  FILE:    HC_CNC_Shield_Test
    DATE:    21/10/14
    VERSION: 0.1
    AUTHOR:  Modificado para proyecto CNC

This is an example sketch which tests some of the functions of the Hobby 
Components CNC shield (HCARDU0086). The sketch will step the X, Y Z, and Aux 
stepper outputs in both directions. It will also report if any of the endstop
or control inputs have been triggered via the serial port. 

WARNING: Ensure that your stepper motors are mechanically disconnected before 
running this sketch as it will not stop drive to the motors should an endstop be 
reached.

If you are using the Aux stepper output you will need to connect the pins labelled
D13 to A-DIR and D12 to A-STEP on the shield.

You may copy, alter and reuse this code in any way you like, but please leave
reference to HobbyComponents.com in your comments if you redistribute this code.
This software may not be used directly for the purpose of selling products that
directly compete with Hobby Components Ltd's own range of products.

THIS SOFTWARE IS PROVIDED "AS IS". HOBBY COMPONENTS MAKES NO WARRANTIES, 
WHETHER EXPRESS, IMPLIED OR STATUTORY, INCLUDING, BUT NOT LIMITED TO, IMPLIED 
WARRANTIES OF MERCHANTABILITY AND FITNESS FOR A PARTICULAR PURPOSE, ACCURACY OR
LACK OF NEGLIGENCE. HOBBY COMPONENTS SHALL NOT, IN ANY CIRCUMSTANCES, BE LIABLE
FOR ANY DAMAGES INCLUDING, BUT NOT LIMITED TO, SPECIAL, INCIDENTAL OR 
CONSEQUENTIAL DAMAGES FOR ANY REASON WHATSOEVER.
*/


#define EN 8      /* Enable pin for all stepper outputs */

#define X_DIR 5   /* Direction pin for X axis */
#define X_STEP 2  /* Step pin for X axis */

#define Y_DIR 6   /* Direction pin for Y axis */
#define Y_STEP 3  /* Step pin for Y axis */

#define Z_DIR 7   /* Direction pin for Z axis */
#define Z_STEP 4  /* Step pin for Z axis */

#define A_DIR 13  /* Direction pin for Aux driver. Requires D13 and A-DIR pins to be shorted */
#define A_STEP 12 /* Direction pin for Aux driver. Requires D12 and A-STEP pins to be shorted */

#define X_ENDSTOP 9   /* X axis endstop input pin */
#define Y_ENDSTOP 10  /* Y axis endstop input pin */
#define Z_ENDSTOP 11  /* Z axis endstop input pin */
#define ABORT A0  /* Abort input pin */
#define HOLD A1   /* Hold input pin */
#define RESUME A2 /* Resume input pin */

int Count = 0; /* Counter to count number of steps made */
boolean Direction = LOW; /* Rotational direction of stepper motors */

/* The setup routine runs once when you press reset: */
void setup() 
{                
  /* Initialize serial */
  Serial.begin(9600);
  
  /* Configure the steper drive pins as outputs */ 
  pinMode(EN, OUTPUT); 
  pinMode(X_DIR, OUTPUT); 
  pinMode(X_STEP, OUTPUT); 
  pinMode(Y_DIR, OUTPUT); 
  pinMode(Y_STEP, OUTPUT); 
  pinMode(Z_DIR, OUTPUT); 
  pinMode(Z_STEP, OUTPUT); 
  pinMode(A_DIR, OUTPUT); 
  pinMode(A_STEP, OUTPUT); 
  
  /* Configure the control pins as inputs with pullups */
  pinMode(X_ENDSTOP, INPUT_PULLUP);
  pinMode(Y_ENDSTOP, INPUT_PULLUP);
  pinMode(Z_ENDSTOP, INPUT_PULLUP);

  pinMode(ABORT, INPUT_PULLUP);
  pinMode(HOLD, INPUT_PULLUP);
  pinMode(RESUME, INPUT_PULLUP);

  /* Enable the X, Y, Z & Aux stepper outputs */
  digitalWrite(EN, LOW); //Low to enable
}

// the loop routine runs over and over again forever:
void loop() 
{
  /* Count one step */
  Count++;
    
  /* If we have reached 500 steps then change the stepper direction and reset the counter */
  if (Count >= 500)
  {
    Direction = !Direction;
    digitalWrite(X_DIR, Direction); // Low = CW 
    digitalWrite(Y_DIR, Direction); // Low = CW 
    digitalWrite(Z_DIR, Direction); // Low = CW 
    digitalWrite(A_DIR, Direction); // Low = CW 
    Count = 0;
  }
    
  /* Step the X, Y, Z, and Aux motors */  
  digitalWrite(X_STEP, HIGH); 
  delay(1); 
  digitalWrite(Y_STEP, HIGH); 
  delay(1); 
  digitalWrite(Z_STEP, HIGH); 
  delay(1);    
  digitalWrite(A_STEP, HIGH); 
  delay(1); 
  
  digitalWrite(X_STEP, LOW);  
  delay(1); 
  digitalWrite(Y_STEP, LOW); 
  delay(1); 
  digitalWrite(Z_STEP, LOW);  
  delay(1); 
  digitalWrite(A_STEP, LOW);  
  delay(1);
  
  /* Check state of inputs */
  if (!digitalRead(X_ENDSTOP)) Serial.println("X-axis end-stop triggered!"); 
  if (!digitalRead(Y_ENDSTOP)) Serial.println("Y-axis end-stop triggered!"); 
  if (!digitalRead(Z_ENDSTOP)) Serial.println("Z-axis end-stop triggered!"); 
  if (!digitalRead(ABORT)) Serial.println("Abort input triggered!"); 
  if (!digitalRead(HOLD)) Serial.println("Hold input triggered!"); 
  if (!digitalRead(RESUME)) Serial.println("Resume input triggered!"); 
}

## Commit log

2022-07-25 Manual y diagrama de CNC Shield plano
    Subida de manual y diagrama
    -CNC Shield Scematics plano
2022-07-25 Add files via upload
    Lista de materiales
    [Materiales.xlsx]
2022-07-25 Eliminacion de .txt
2022-07-25 Layout físico arduino UNO
2022-07-25 Add files via upload
    Diagramas de las piezas utilizadas para realizar la CNC.
    Se adjuntan:
    -La base del motor del eje Z junto su tapa
    -La pieza de soporte de la CNC
2022-07-25 Lista de materiales y precios
    [Materiales.xlsx]
2022-07-25 Ensamble CNC
    Piezas y ensamble
    [Axis Z soporte motor.SLDPRT, Ball Bearing 8 x 16 x 5.SLDPRT, Base Madera.SLDPRT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]
2022-08-04 Actualizacion de README-1
    Diseño de README
2022-08-05 Inicio de desarrollo
    Desarrollo hasta elección del proyecto
2022-08-05 Add files via upload
    Diagramas para los soportes del motor y el rodamiento del eje X
2022-08-05 Actualización desarrollo
    Se agregaron los puntos de investigación, diseño, compra de materiales y corte de perfiles
2022-08-21 Imagenes
    Imagenes del armado de la maquina CNC
    [Presupuesto.xlsx]
2022-08-22 Imagenes, SRC y Diagramas
    Se actualizan las carpetas con imagenes, diagrama, y informacion acerca de la CNC
    [Codigo para arduino uno Shield CNC GRBL v3.0.txt]
2022-08-22 Update Diagrama de conexiones.png
2022-08-22 Create Ensamble De la CNC
2022-08-22 Create Proceso de lubricacion
2022-08-22 Create Realización de pruebas
2022-08-22 Create Desarrollo del ensamble de la CNC
2022-08-22 Versión 1.1 del diseño
    Actualización del diseño CAD
    [Angulo de soporte.SLDPRT, Angulo perfil X-Z.SLDPRT, Axis Z soporte motor.SLDPRT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]
